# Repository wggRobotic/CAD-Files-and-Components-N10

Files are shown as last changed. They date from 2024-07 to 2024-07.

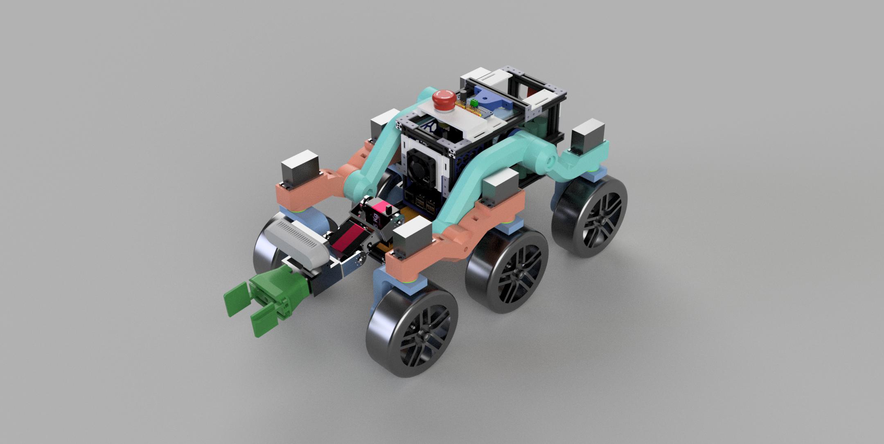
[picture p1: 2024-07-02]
Robot/N-10_frontview.jpg

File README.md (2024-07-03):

# Robot components

Here you will find all the essential components of our robot N-10 available as .stl and .stp files, enabling anyone to build and modify the robot. 

Our robot is a rover featuring a Rocker-Bogie suspension system, inspired by the Mars rovers and the open-source project [Stair Climbing Rover](https://www.printables.com/model/194299-stair-climbing-rover) by WildWilly. The components have been modified, supplemented, and completely redesigned to suit our specific needs.

N-10_frontview

## Main Body Structure

The main body of the rover is assembled using aluminum extrusions from [Makerbeam](https://www.makerbeam.com/makerbeam-makerbeam-regular-starter-kit-black.html). This design choice ensures a stable, robust, yet lightweight framework for the robot.

Most of the other components are designed for 3D printing and can be assembled using M3, M2.5, or M2 machine screws. For additional stability and support, the servomotors, motor mounts, and wheel hubs are anchored in the plastic using [M3 heat-set inserts](https://www.amazon.de/ruthex-Gewindeeinsatz-St%C3%BCck-Gewindebuchsen-Kunststoffteile/dp/B08BCRZZS3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).

Material Recommendations:

  + Load-bearing components: PETG
  + Decorative/Chassis components: PLA (sufficient for parts that do not bear heavy loads)

Enjoy building and customizing your own robot!

N-10_backview

## Wheel Control and Alignment

The control and alignment of each wheel are managed by Hobby servomotors of the type MG996 [amazon link](https://www.amazon.de/AZDelivery-Digital-Getriebe-Hubchrauber-Flugzeug/dp/B07H89JH74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). These servomotors are addressed via I2C through an Adafruit PCA9685 servo board.

Radsteuerung

The wheel and motor mounts, as well as the wheel hubs, are specially designed for our purposes and printed from PETG. Due to space constraints, the motor mounts needed to be fabricated from steel to prevent rotation, as a printed part with a thickness of 2mm would not provide the necessary strength.

Halterung

Radaufnahme

## Motors and motorcontrol
Our six wheels are powered by Faulhaber DC motors with planetary gearboxes [2224U018S R IEH2-512 22GPT 44:1](https://www.faulhaber.com/de/produkte/serie/22gpt/), generously provided by Faulhaber for this project. Motor control and regulation, as well as the power supply for other components, are handled by a Kinematics Kit, kindly provided by [EduArt Robotik](https://www.eduart-robotik.com/). This kit is designed to be mounted on a Raspberry Pi 4 or [5](https://www.berrybase.de/raspberry-pi-5-8gb-ram) and can be expanded modularly. The basic components of the kit include:

+ Adapter Board either directly pluggable onto a Raspberry Pi 4/5 or as a standalone EduArt Ethernet controller board, with which you can connect any computer with an Ethernet interface. This gives you the freedom to build the computing power into your robot that you need for your desired application. This board is supplied via the socket strips, i.e. a circuit board with the appropriate sockets for a power supply unit or a battery should be used. The possible input voltage Vin is 12V to 55V. Depending on how many motors are connected, the power supply must be able to supply higher currents. High-current batteries are recommended for operating a robot (min. 8A).

+ Motorcontrollers can be plugged in directly. This allows you to control the speed of 1 to 8 motors. The motor controllers are available in two versions, single-channel or dual-channel. Up to four motor controllers can be used, i.e. it is possible to use 1 to 4 larger motors (IRMS up to 5A) or 1 to 8 smaller motors (IRMS up to 2.5A). The dielectric strength of the single-channel motor controllers is 55V. The dielectric strength of the dual-channel motor controllers is 35V.

+ The Power Management Module takes over the charge control of a 19.2V NiMH battery pack and also offers an on/off logic. Temperature monitoring of the battery uses an integrated 6.8kOhm NTC. Never connect a battery other than the one supplied by EduArt.
    
+ The Auxiliary Power Supply Module provides additional voltage levels with which you can supply additional devices. The permissible operating voltage is between 15V and 36V.

Warning: The Raspberry single-board computer is supplied directly via the socket connectors. Never connect an external power supply for the Raspberry via USB-C.

Free_Kinematics_Kit_1920

Free_Kinematics_Kit_Electrical_Interface_Desc_1920

## Power Supply

The power and voltage supply is provided by a NiMH, 19.2V, 4.5 Ah battery pack. Although Nickel-Metal Hydride batteries are significantly heavier than comparable Li-ion batteries, they have much lower risks of fire and explosion. Additionally, these batteries are more maintenance-friendly, which outweighs the disadvantages for us. For powering the Raspberry Pi 5 and the servomotors, the voltage is stepped down using DC-DC converters, as described in the Motor Control section. Specifically, for powering the servomotors, we use an additional DC-DC converter [UWS-5/10-Q12P-C](https://www.digikey.de/de/products/detail/murata-power-solutions-inc/UWS-5-10-Q12P-C/10427628) on our board that supplies the servos on the PCA9685 board with 5V at 10A as an external power source.

## Cameras and Camera Feed

The robot is equipped with three cameras:

+ Front Cameras: Mounted on the robot arm are an [Intel RealSense D435](https://www.amazon.de/Intel-RealSense-82635AWGDVKPRQ-Erfassung-beweglicher/dp/B07BLS5477) and a [Waveshare MLX90640](https://www.amazon.de/Waveshare-MLX90640-Communicating-Interface-Raspberry/dp/B07ZKK8QWY) thermal imaging camera, both facing forward.
+ Rear Camera: A USB camera module [OV2710](https://www.berrybase.de/usb-2.0-kameramodul-2-megapixel-ov2710-sensor-1450-low-light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) is used as a rearview camera.

All cameras have been recycled from older projects.

In our GUI, users can switch between the different camera feeds with the press of a button.

## Simple Robot Arm Assembly

This section provides a brief description of the simple robot arm mounted on the N10 robot. 

Arm_topview

The main components include:

+ Two powerful [Servomotors](https://www.amazon.de/ANNIMOS-Servomotor-Drehmoment-Vollmetallgetriebe-Montagehalterungen/dp/B0C69NNP9P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) with aluminum brackets: These form the basic structure of the arm. 

+ Camera Module: Equipped with an [Intel-RealSense D435](https://www.amazon.de/Intel-RealSense-82635AWGDVKPRQ-Erfassung-beweglicher/dp/B07BLS5477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) camera and a thermal imaging camera module ([Waveshare MLX90640](https://www.amazon.de/Waveshare-MLX90640-Communicating-Interface-Raspberry/dp/B07ZKK8QWY)).
  
+ Gripper: A simple gripper controlled by a [9g servomotor](https://www.amazon.de/Miuzei-Hubschrauber-Helikopter-Fahrzeugmodelle-Steuerung/dp/B07KPS9845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).
  
+ Control: The arm is controlled via I2C using an [Adafruit PCA9685 servo board](https://www.amazon.de/PCA9685-16-Kanal-12-Bit-Arduino-Robort/dp/B07Y9PTY12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).

## Component-list

Component | Unit price | Quantity | Total price | Note
-------- | :--------: | :--------: | :--------: | --------
MG996 - Servomotor   | 6.00 €   | 6 | 36.00 €   | [Amazon](https://www.amazon.de/AZDelivery-Digital-Getriebe-Hubchrauber-Flugzeug/dp/B07H89JH74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)
ANNIMOS 25kg Servomotor   | 29.98 €   | 2 | 59.96 €   | [Amazon](https://www.amazon.de/ANNIMOS-Servomotor-Drehmoment-Vollmetallgetriebe-Montagehalterungen/dp/B0C69NNP9P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)
9g Micro Servomotor  | 2.00 €   | 1 | 2.00 €   | [Amazon](https://www.amazon.de/Miuzei-Hubschrauber-Helikopter-Fahrzeugmodelle-Steuerung/dp/B07KPS9845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)
EduArt Kinematics Kit  | 786.75 €   | 1 | 786.75 €  | [Eduart Robotik](https://www.eduart-robotik.com/)
Faulhaber DC motors with planetary gearboxes  | 209.20 €   | 6 | 1255.20 €   | [2224U018S R IEH2-512 22GPT 44:1](https://www.faulhaber.com/de/produkte/serie/22gpt/)
Raspberry Pi 5 8Gb  | 86.50 €   | 1 | 86.50 €   | [berrybase](https://www.berrybase.de/raspberry-pi-5-8gb-ram) 
Intel RealSense D435 | 343.92 € | 1 | 343.92 € | [Amazon](https://www.amazon.de/Intel-RealSense-82635AWGDVKPRQ-Erfassung-beweglicher/dp/B07BLS5477?th=1)
Waveshare MLX90640 | 71.99 € | 1 | 71.99 € | [Amazon](https://www.amazon.de/Waveshare-MLX90640-Communicating-Interface-Raspberry/dp/B07ZKK8QWY)
USB camera module OV2710 | 33.40 € | 1 | 33.40 € | [berrybase](https://www.berrybase.de/usb-2.0-kameramodul-2-megapixel-ov2710-sensor-1450-low-light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)
PCA9685 Servomotor Drive Module | 6.50 € | 1 | 6.50 € | [Amazon](https://www.amazon.de/PCA9685-16-Kanal-12-Bit-Arduino-Robort/dp/B07Y9PTY12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)
Black Starter Kit Regular MakerBeam  | 117.95 € | 1 | 117.95 € | [Makerbeam](https://www.makerbeam.com/makerbeam-makerbeam-regular-starter-kit-black.html)
Maschine screws (M2, M2.5 M3) | 24.65 € | 1 | 24.65 € | [Amazon](https://www.amazon.de/Edelstahl-Sechskopf-Knopf-Schrauben-Unterlegscheiben-Sortiment-Aufbewahrung/dp/B07FPGNTXD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)
Heat-Set Inserts | 8.99 € | 1 | 8.99 € | [Amazon](https://www.amazon.de/ruthex-Gewindeeinsatz-St%C3%BCck-Gewindebuchsen-Kunststoffteile/dp/B08BCRZZS3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)
|  | |**TOTAL:** | 2833.81 € |

The total price of all components is very high, but most of the components are high-quality products that can usually be replaced very easily with comparable, significantly cheaper components. For example, simpler [Pololu motors](https://www.pololu.com/category/272/24v-37d-metal-gearmotors) can be used instead of Faulhaber motors. It should also be mentioned at this point that some of these components, like the Intel-Realsense D435, were already available from previous projects at our school and have now found a new use. We would also like to thank Faulhaber, EduArt Robotik and Siemens for making their components available to us free of charge.

## Software Control
For more details on software control, please refer to the software section.

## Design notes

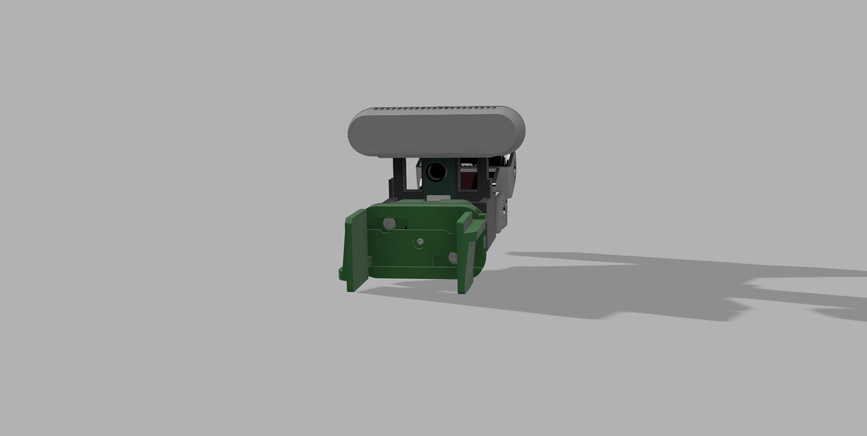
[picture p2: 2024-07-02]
Robot-Arm/Arm_frontview.jpg

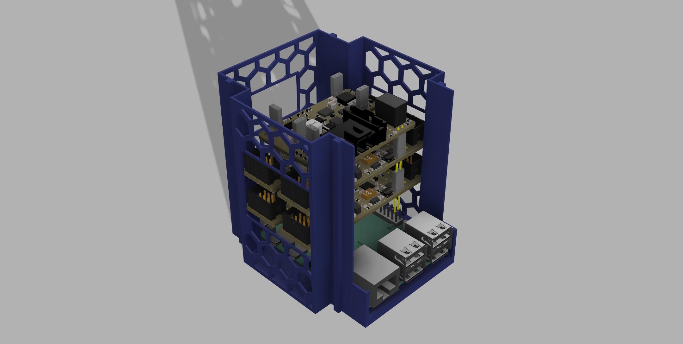
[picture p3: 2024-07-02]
Robot/Motorcontroller_Unit/Motorcontrol_unit.jpg

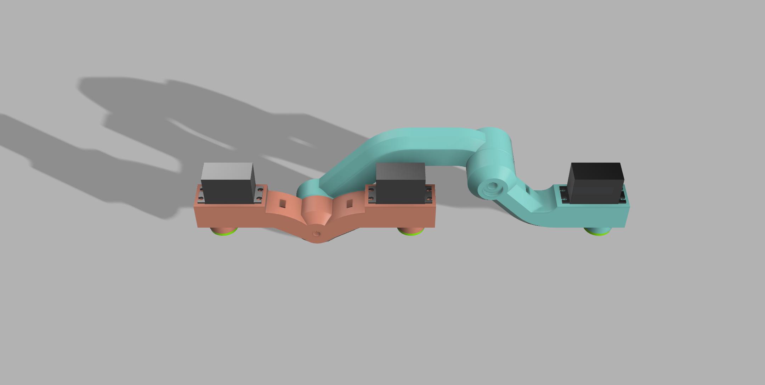
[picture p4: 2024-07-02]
Robot/Rocker_Bogie_Suspension/Rocker_Bogie_Suspension_Right.jpg

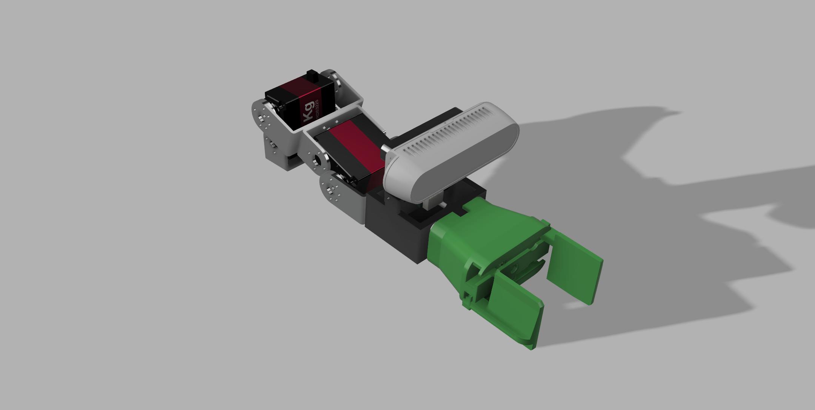
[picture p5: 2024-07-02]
Robot-Arm/Arm_topview.jpg

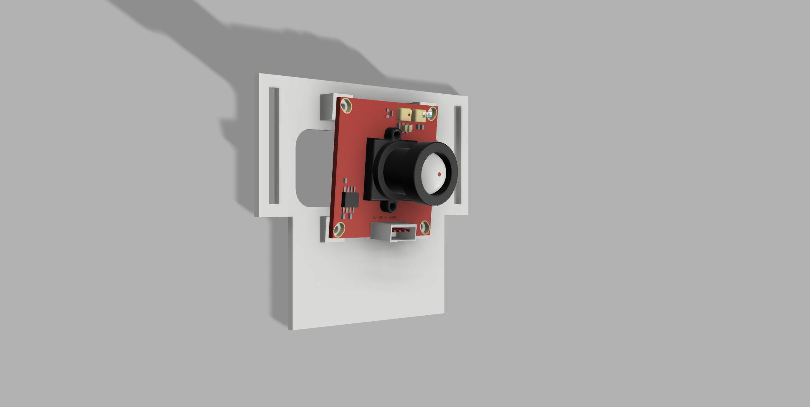
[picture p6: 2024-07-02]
Robot/Back_Camera/Back_Camera.jpg

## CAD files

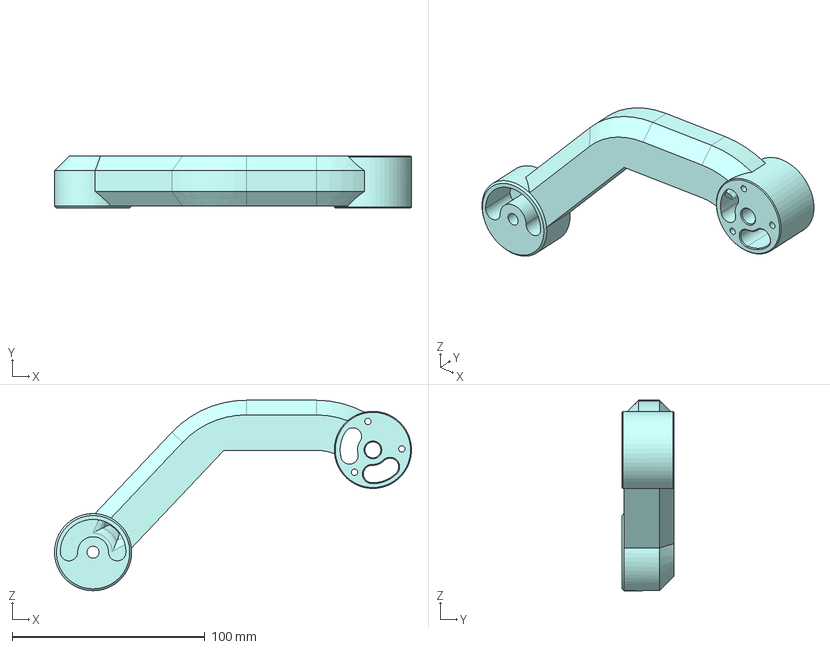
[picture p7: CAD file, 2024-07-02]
Robot/Rocker_Bogie_Suspension/Components/Main Arm.step
185.0 x 27.0 x 98.7 mm

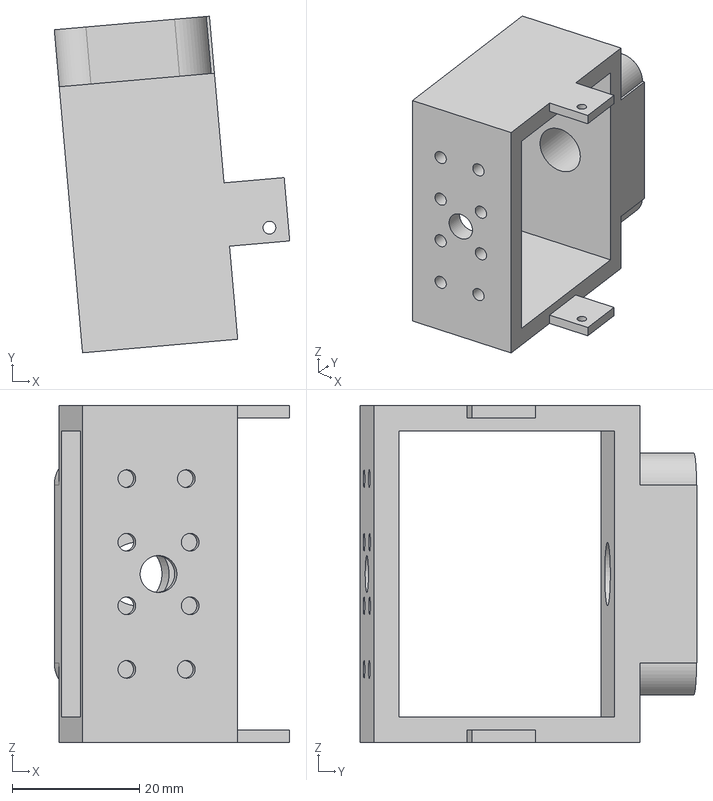
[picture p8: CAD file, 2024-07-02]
Robot-Arm/Components/Arm_Bracket.step
37.0 x 52.9 x 53.0 mm

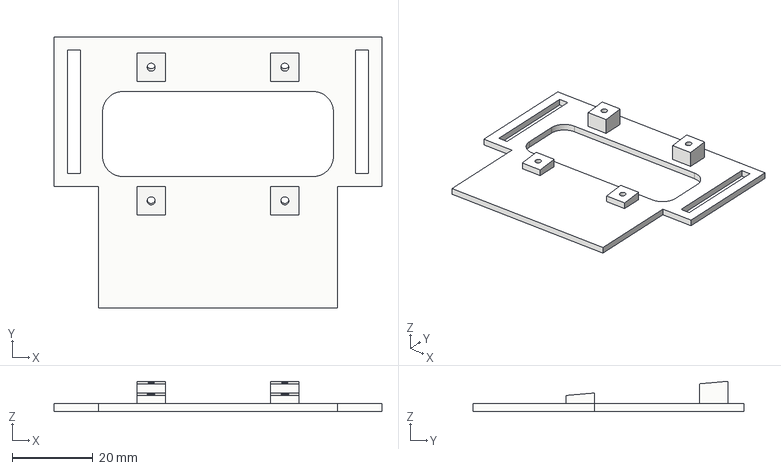
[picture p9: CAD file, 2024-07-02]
Robot/Back_Camera/Components/Back_Camera_Mount.step
81.0 x 67.0 x 7.51 mm

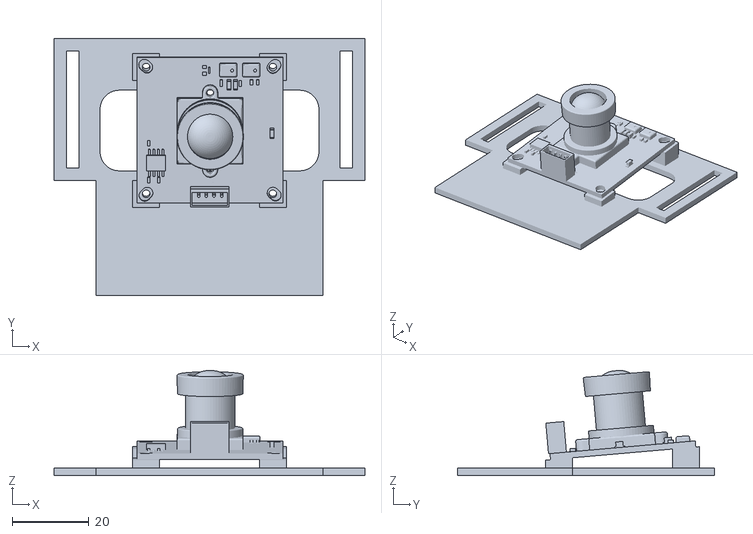
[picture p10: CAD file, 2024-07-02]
Robot/Back_Camera/Kamera hinten_5Grad v4.stl
81.0 x 67.0 x 27.4

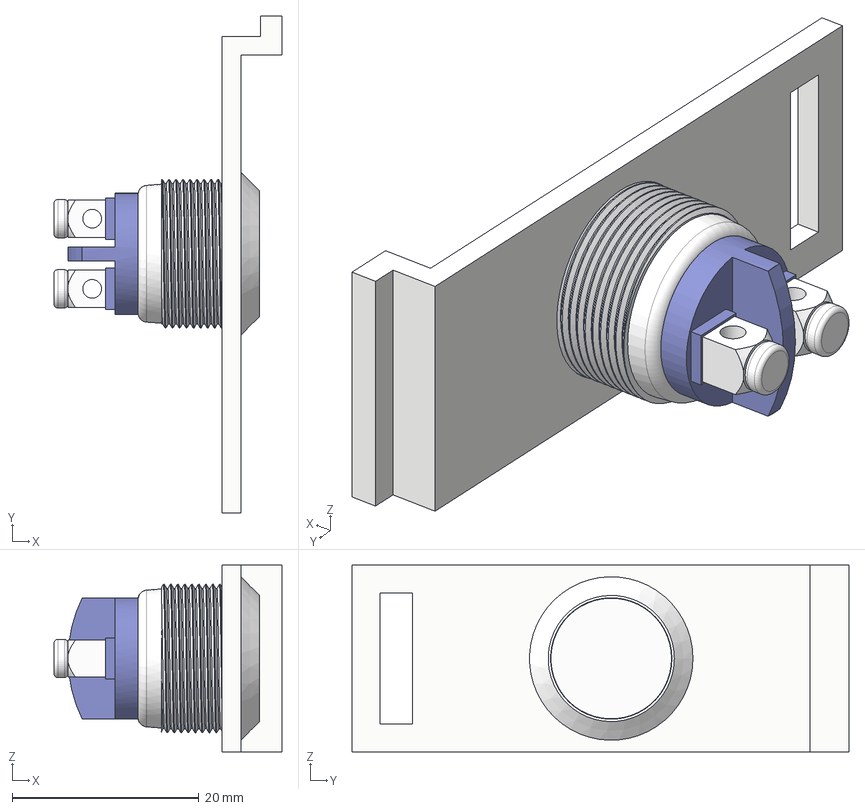
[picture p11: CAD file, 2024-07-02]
Robot/Chassis_Components/Taster.step
24.4 x 53.2 x 20.0 mm

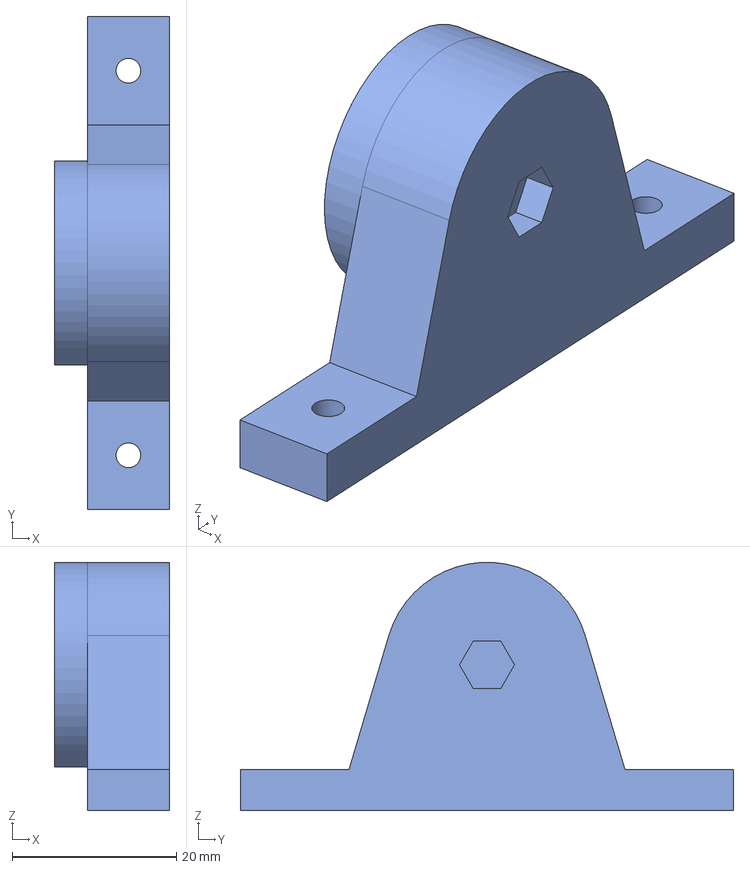
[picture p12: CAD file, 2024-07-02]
Robot/Differential_Mounting/Components/Differential_mount_holder.step
14.0 x 60.0 x 30.2 mm

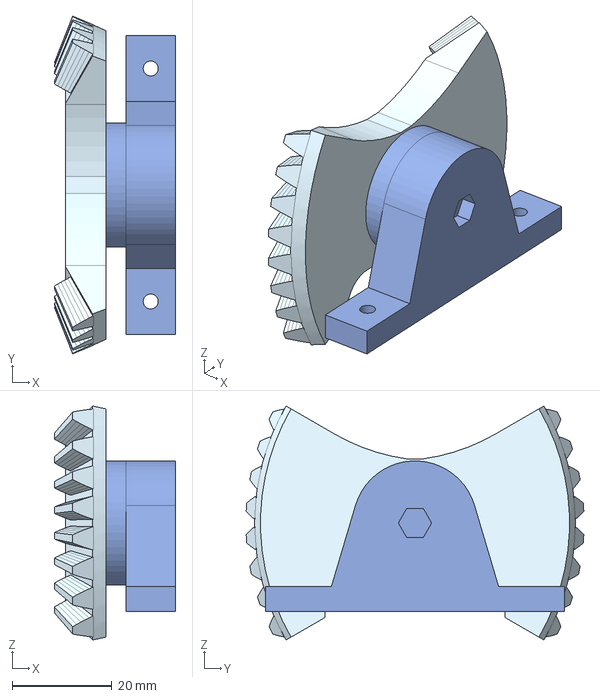
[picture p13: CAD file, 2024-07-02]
Robot/Differential_Mounting/Differential_mount.step
24.3 x 67.8 x 47.0 mm

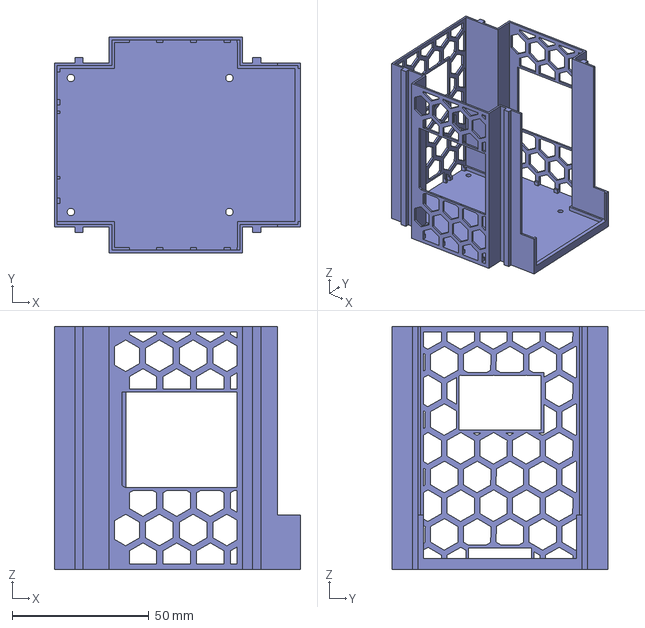
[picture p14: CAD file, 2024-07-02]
Robot/Motorcontroller_Unit/Modul_cage.step
90.0 x 79.0 x 89.0 mm

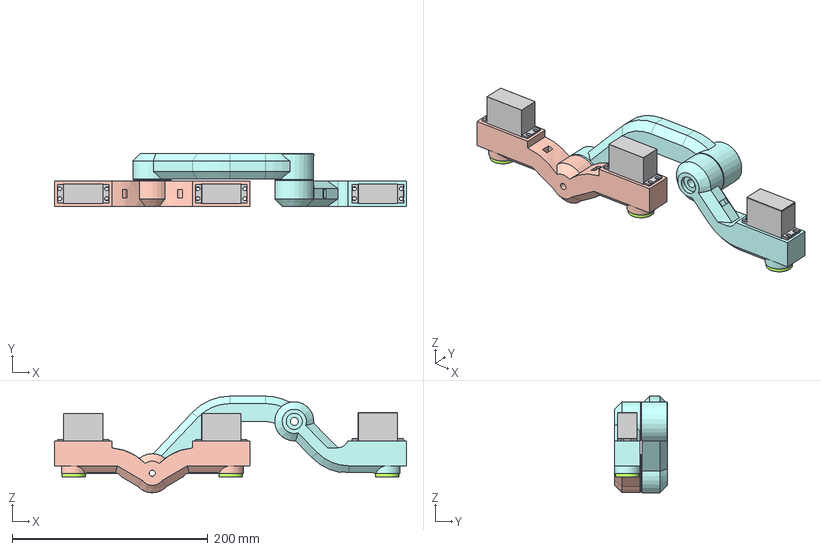
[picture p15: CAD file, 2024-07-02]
Robot/Rocker_Bogie_Suspension/Rocker_Bogie_Suspension_Right v5.step
359.5 x 54.0 x 98.7 mm
Main Arm
Front_arm
Endstop
MG-996R x 4
Coupler
Coupler_1
Coupler_2

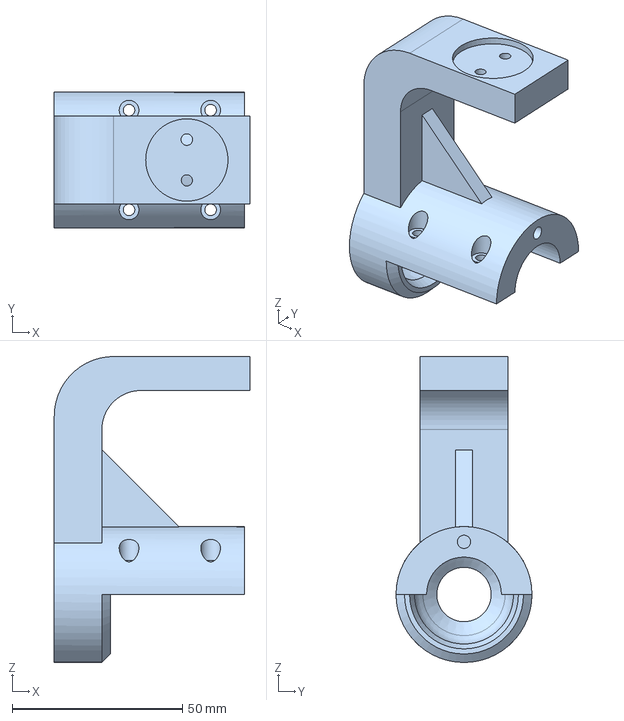
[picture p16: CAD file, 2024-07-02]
Robot/Wheel_System/Components/Motor_arm.step
57.5 x 40.0 x 90.0 mm

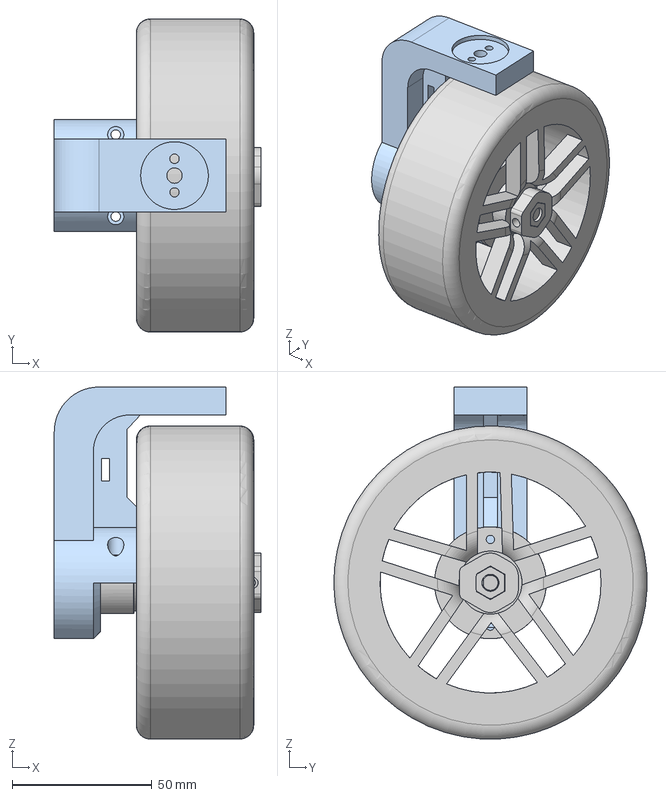
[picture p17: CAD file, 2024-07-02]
Robot/Wheel_System/Wheel_System.step
73.8 x 111.9 x 125.8 mm
12x_motor_mount
6x_motor_arm1
Motorhalterung
Komponente1
Radaufnahme
RC_Reifen_1/8

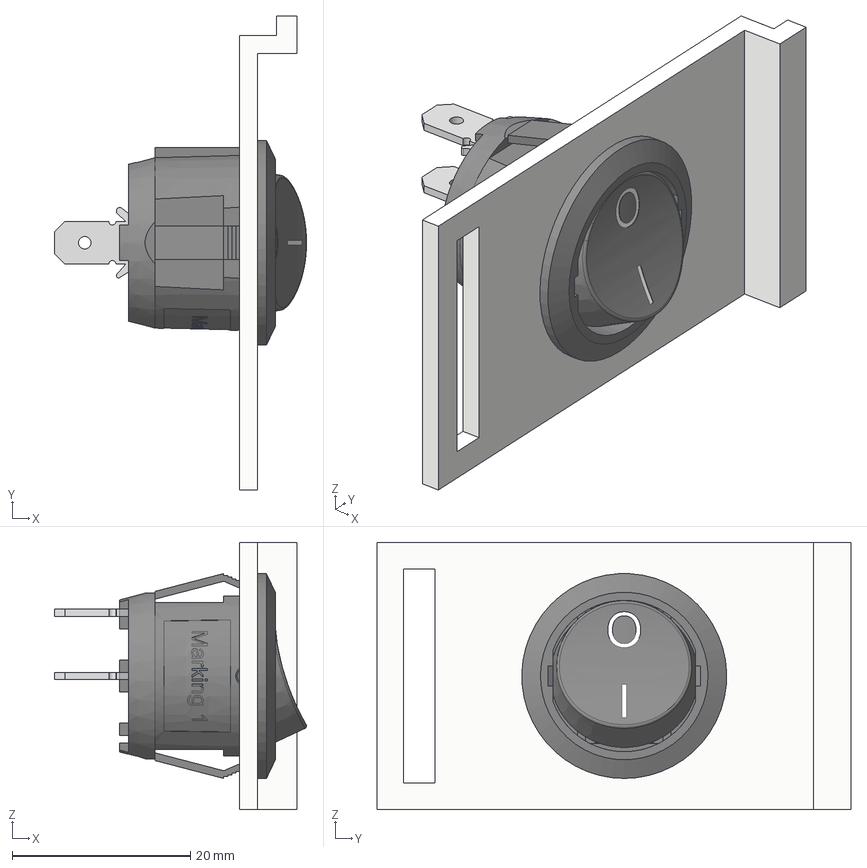
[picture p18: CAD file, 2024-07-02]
Robot/Chassis_Components/Kippschalter.step
28.3 x 53.2 x 30.0 mm
Frame
Actuator

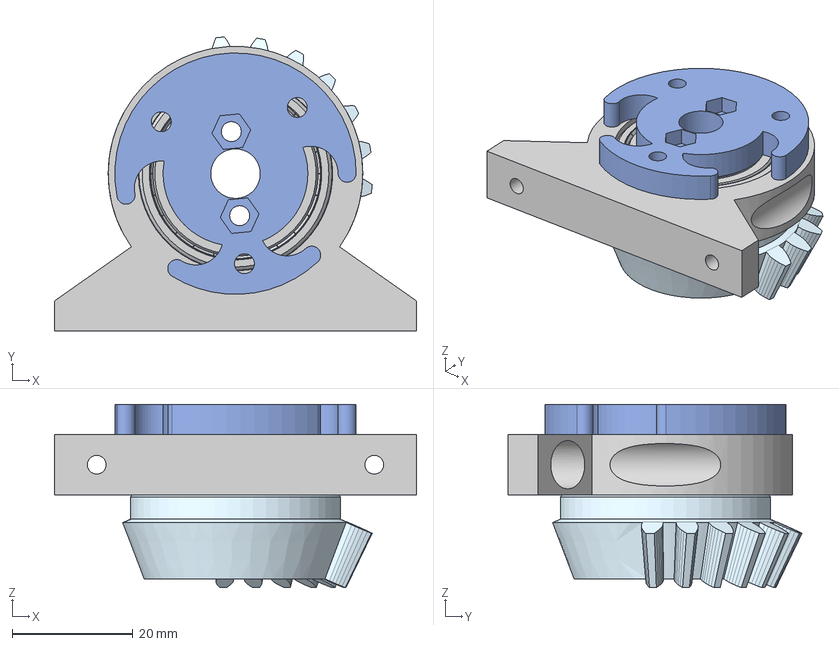
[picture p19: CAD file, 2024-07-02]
Robot/Differential_Mounting/Axle_mount.step
60.0 x 48.8 x 30.4 mm
5972K157_Ball Bearing
Achsenhalterung_neu
Arm_coupler
Bevel_gear

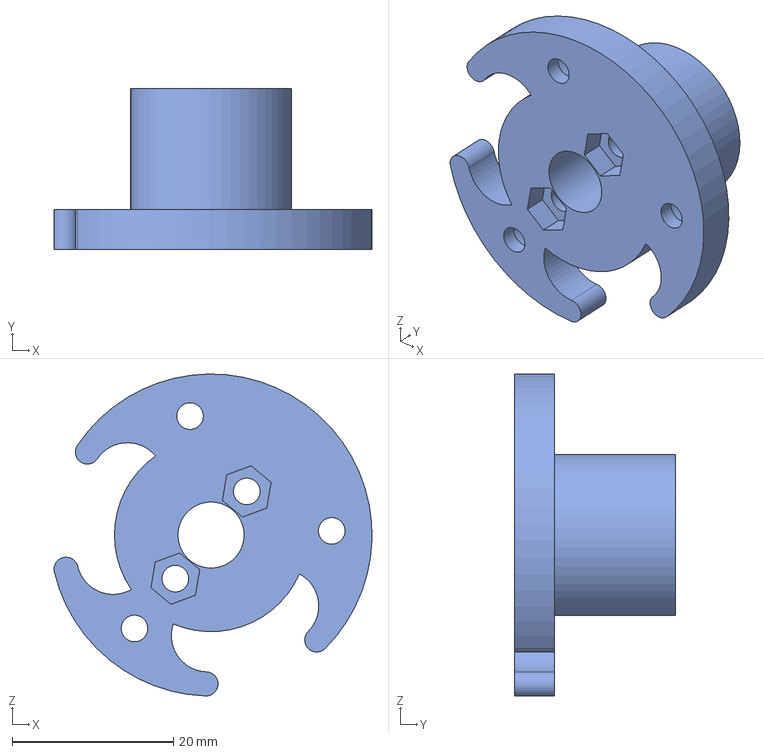
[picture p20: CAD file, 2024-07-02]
Robot/Differential_Mounting/Components/Arm_coupler.step
39.5 x 20.0 x 40.0 mm

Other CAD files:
Robot/Back_Camera/Back_Camera.step
Robot/Rocker_Bogie_Suspension/Components/Back_arm.step
Robot/Wheel_System/Components/Coupler.step
Robot/Chassis_Components/Body.step
Robot-Arm/Components/Arm_Bracket.stl
Robot/Back_Camera/Components/Back_Camera_Mount.stl
Robot/Chassis_Components/Kippschalter.stl
Robot/Chassis_Components/Ladebuchse.step
Robot/Chassis_Components/Ladebuchse.stl
Robot/Chassis_Components/Notaus.stl
Robot/Chassis_Components/Taster.stl
Robot/Differential_Mounting/Axle_mount.stl
Robot/Differential_Mounting/Components/Arm_coupler.stl
Robot/Differential_Mounting/Components/Axial_Mount_Bearing.stl
Robot/Differential_Mounting/Components/Axial_mount_bearing.step
Robot/Differential_Mounting/Components/Bevel_gear.step
Robot/Differential_Mounting/Components/Bevel_gear.stl
Robot/Differential_Mounting/Components/Differential_mount_holder.stl
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

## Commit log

2024-06-16 New Robot Arm Files uploaded
2024-07-02 Added Components
    Added all robot romponets as .stl and .step
    [Arm_Bracket.step, Arm_Bracket.stl, Arm_coupler.step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]
